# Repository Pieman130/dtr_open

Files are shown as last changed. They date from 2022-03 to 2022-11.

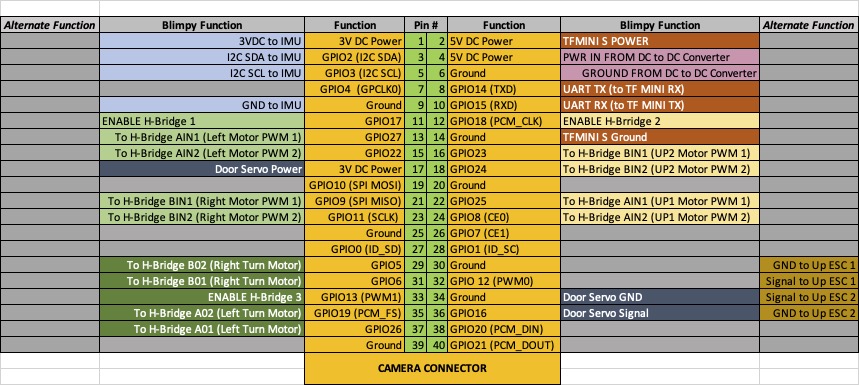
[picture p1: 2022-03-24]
images/Rpi2_pinout.jpg

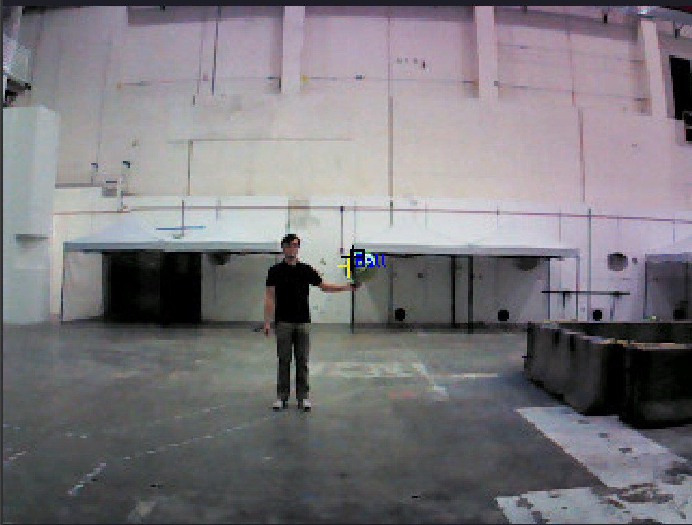
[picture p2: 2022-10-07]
images/Color Detection Metrics Videos/Test Example Photo.png

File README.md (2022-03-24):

More info in wiki: [DTR Wiki](https://github.iu.edu/DTR/dtr/wiki)

`blimpy.py` is the main Blimp script

`IMU_test.py` to run simple tests to ensure BNO055 IMU is functioning

`LIDAR_test.py` tests for TFMini lidar using UART connection

`manual_control.py` to operate blimp with only PS3 controller (no autonomy)  Note: deadman switch is disabled 

**NOTE: the BNO055 library requires two updates:**
1) Ensure software I2C is enabled and HW I2C is disabled on the raspberry pi
	1) modify `/boot/config.txt` to include this line:
	
	`dtoverlay=i2c-gpio,bus=3,i2c_gpio_sda=23,i2c_gpio_scl=24`
	
	2) comment this line out if not already done:

	`dtparam=i2c_arm=on`

2) You may need to modify `bno055.py` to add support for software i2c bus.  On line 196 `self._bus = smbus.SMBus(1)` change the 1 to a 3

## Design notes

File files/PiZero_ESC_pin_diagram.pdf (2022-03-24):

Alternate Function | Blimpy Function | Function | Pin # | Function | Blimpy Function | Alternate Function
| 3VDC to IMU | 3V DC Power | 1 | 2 | 5V DC Power | TFMINI S POWER | Additional wire to Vin Ultrasonic Sensor
| I2C SDA to IMU | GPIO2 (I2C SDA) | 3 | 4 | 5V DC Power | PWR IN FROM DC to DC Converter
| I2C SCL to IMU | GPIO3 (I2C SCL) | 5 | 6 | Ground | GROUND FROM DC to DC Converter
| | GPIO4 (GPCLK0) | 7 | 8 | GPIO14 (TXD) | UART TX (to TF MINI RX)
| GND to IMU | Ground | 9 | 10 | GPIO15 (RXD) | UART RX (to TF MINI TX)
| | GPIO17 | 11 | 12 | GPIO18 (PCM_CLK)
| | GPIO27 | 13 | 14 | Ground | TFMINI S Ground
| Door Servo Signal | GPIO22 | 15 | 16 | GPIO23 | Ultrasonic TRIG
| Door Servo Power | 3V DC Power | 17 | 18 | GPIO24 | Ultrasonic ECHO
| | GPIO10 (SPI MOSI) | 19 | 20 | Ground
| | GPIO9 (SPI MISO) | 21 | 22 | GPIO25
| | GPIO11 (SCLK) | 23 | 24 | GPIO8 (CE0)
| Door Servo GND | Ground | 25 | 26 | GPIO7 (CE1) | Thrust Motor
| | GPIO0 (ID_SD) | 27 | 28 | GPIO1 (ID_SC)
| | GPIO5 | 29 | 30 | Ground
| | GPIO6 | 31 | 32 | GPIO 12 (PWM0) | Altitude Front Motor
| | GPIO13 (PWM1) | 33 | 34 | Ground
| | GPIO19 (PCM_FS) | 35 | 36 | GPIO16 | Altitude Rear Motor
| | GPIO26 | 37 | 38 | GPIO20 (PCM_DIN) | Steer Motor
| | Ground | 39 | 40 | GPIO21 (PCM_DOUT) | Steer Servo
CAMERA CONNECTOR

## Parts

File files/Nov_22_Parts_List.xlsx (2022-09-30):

Need | Item | Quantity Rqd* | Quantity OH | Source | Note
 | Store Purchased
X | Small Carbon Fiber Rods | 13 | 8 | https://www.amazon.com/gp/product/B07P81VC34/ref=sw_img_1?smid=A1THAZDOWP300U&th=1 | Come in packes of 10
 | Large Carbon Fiber Rods | 7 | 11 | https://www.amazon.com/gp/product/B07V2J6YSR/ref=ppx_yo_dt_b_asin_title_o07_s00?ie=UTF8&th=1 | Come in packs of 4
X | 1200mAh Battery | 1 | 1 | https://www.amazon.com/dp/B09K7VLDN5?psc=1&ref=ppx_yo2ov_dt_b_product_details | Come in packs of 2
 | Servo | 1 | 2 | https://www.amazon.com/FLASH-HOBBY-Steering-Interface-Aircraft/dp/B08NPHG99D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 | We actually have a lot more in the drawer
 | RC Receiver | 1 | 1 | https://www.amazon.com/gp/product/B01N5INCBH/ref=ppx_yo_dt_b_asin_title_o07_s01?ie=UTF8&psc=1 | 1 Rcvr shared between craft
 | OpenMV Carmera | 1 | 1 | https://www.sparkfun.com/products/18982 | vers H7 (out of stock most places)
 | ESC | 3 | 5 | https://www.amazon.com/gp/product/B09F3G4KNB/ref=ppx_yo_dt_b_asin_title_o01_s00?ie=UTF8&psc=1 | Come in packs of 4
 | Motors | 3 | 4 | https://www.amazon.com/gp/product/B07XR8GYT5/ref=ppx_yo_dt_b_asin_title_o01_s02?ie=UTF8&psc=1 | Come in packs of 4
 | Props | 3 | 10+ | https://www.amazon.com/gp/product/B087CX2JYG/ref=ppx_yo_dt_b_asin_title_o01_s02?ie=UTF8&psc=1 | Come in packs of 16
 | Lidar | 1 | 2 | https://www.amazon.com/dp/B08D1XVRV5?aaxitk=5ca1cb0fbe332688bafaf63f109873fa&hsa_cr_id=7103712130501
 | JST-PH 2,0 Connectors | 4 | 5+ | https://www.amazon.com/Upgraded-Connector-Battery-Inductrix-Eachine/dp/B07NWD5NTN?s=electronics | Come in packs of 5
 | PixRacer | 1 | 1 | https://store.mrobotics.io/mRo-PixRacer-R14-Official-p/auav-pxrcr-r14-mr.htm | Out of stock everywhere
 | Wire (various colors) | As Needed | Probably Enough | https://www.amazon.com/Fermerry-Stranded-Silicone-Cables-Electrical/dp/B089CP9N98 | Should have enough of each color on hand
 | GH 1.25 Connectors | 1 | 1 | https://www.amazon.com/gp/product/B07PBHN7TM/ref=ppx_yo_dt_b_asin_title_o05_s06?ie=UTF8&psc=1 | Still have half the box on hand
 | DC to DC Converter | 1 | 1 | https://www.amazon.com/Converter-DROK-Adjustable-Transformer-Stabilizer/dp/B08Q3PMJTT | Original purchased model no longer available
X | Blue Balloons | 4 | 0 | https://balloonsfast.com/big-round-balloons-mylar-36-inch-blue-foil-circle-balloon-12679.html
 | Red Balloons | 0 | 4 | https://www.balloons123.com/products/36-round-ruby-red-foil-foil-balloon?variant=422858981403&currency=USD
 | 3D printed parts
 | Catcher - "Y" corners | 5 | 5 | collin_corner_connector1 v2.stl
 | Catcher - "T" connector | 4 | 6 | Collin_Support Connector v1 v2.stl
 | Catcher - Straight Connector | 5 | 10 | Collin_Straight Connector v1 v3.stl
 | Large Ballon Coupler | 4 | 4 | ??
 | Small Balloon Coupler | 2 | 4 | balloon coupler v4.stl
X | Basket to Balloon mount | 4 | 0 | Catcher Mount v1.stl
X | Wire Clips | 8 | 1 | wire clips v2.stl
 | Thrust/Yaw Mount | 1 | 1 | Thrust_Yaw Mount v5.stl
X | Lidar Mount | 1 | 0 | TFMini mount v2.stl
X | Battery Mount | 1 | 0 | Collin_Battery_Holder_Square v2 v2.stl
 | Pixracer Mount | 1 | 1 | PixRacer Mount v2.stl
 | Up Motor Mount | 1 | 4 | flat_mount.stl
X | OpenMV Mount | 1 | 0 | openMV Mount v2.stl
X | ESC Mount | 3 | 2 | esc clip v2.stl
 | Large Tube Coupler | 2 | 6 | ??
 | Large "X" Coupler | 2 | 5 | ??
 | Custom PCB Parts
 | OpenMV Shield | 1 | 1 | Custom made - TODO - breakout individual parts
 | IR Detector | 1 | 1 | Custom made - TODO breakout individual parts
 | *Quantity Rqd is per craft

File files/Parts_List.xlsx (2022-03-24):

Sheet: Basic_Kit
Component | Qty | Cost | Subotal | Link | Min Qty
Camera | 1 | 69.95 | 69.95 | https://www.robotshop.com/en/openmv-cam-h7-r2-image-sensor.html | 1
Camera | 1 | 0 | 0 | Alternate Cameras?
Servos | 1 | 12.65 | 12.65 | https://www.amazon.com/FLASH-HOBBY-Steering-Interface-Aircraft/dp/B08NPHG99D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 | 1
Motors | 1 | 9.95 | 9.95 | https://www.amazon.com/4pcs-Coreless-Brushed-Motor-7x16mm/dp/B08LV5HK8D | 1
Props | 1 | 11.99 | 11.99 | https://www.amazon.com/Propellers-Replacement-Eachine-Inductrix-Quadcopter/dp/B079DP3V42 | 1
Remote | 1 | 12.99 | 12.99 | https://www.amazon.com/VOYEE-PS3-Controller-Wireless-Rechargable/dp/B07TYR1MDV | 1
Tape | 1 | 10.99 | 10.99 | https://www.amazon.com/Double-Double-Sided-Adhesive-Scrapbook-Display/dp/B087QYVCPW | 1
Driver | 1 | 7.49 | 7.49 | https://www.pololu.com/product/2135 | 1
Connectors | 1 | 21.99 | 21.99 | https://www.amazon.com/Pre-Crimped-Connectors-SPRacingF3-Omnibus-Silicone/dp/B07PDQKHJ2 | 1
Connectors | 1 | 6.99 | 6.99 | https://www.amazon.com/gp/product/B013JRWCBU | 1
Connectors | 1 | 7.59 | 7.59 | https://www.amazon.com/Micro-2-Pin-Connector-100Mm-Female/dp/B01DUC1I7S?s=electronics | 1
Connectors | 1 | 20.99 | 20.99 | https://www.amazon.com/Pre-Crimped-Connectors-Pixhawk2-Pixracer-Silicone/dp/B07PBHN7TM | 1
Conenctors | 1 | 12.19 | 12.19 | https://www.amazon.com/Connectors-1-25MM-Female-Connector-Cables/dp/B073WPQLVX?s=electronics | 1
Controller | 1 | 10 | 10 | https://www.mouser.com/ProductDetail/Espressif-Systems/ESP32-DevKitC-32D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 | 1
Controller | 1 | 9.59 | 9.59 | https://www.amazon.com/Raspberry-Microcontroller-Development-Dual-Core-Processor/dp/B08TN4VLN7
Controller | 1 |  | 0 | Alternate Microcontrollers?
Battery | 6 | 7.95 | 47.7 | https://www.adafruit.com/product/1578 | 4
Charger | 2 | 6.95 | 13.9 | https://www.adafruit.com/product/1905 | 2
Air Swimmer | 4 | 39.99 | 159.96 | https://www.amazon.com/Air-Swimmer-Inflatable-Flying-Shark/dp/B00658LN3E | 2
PI Camera | 1 | 13.99 | 13.99 | https://www.amazon.com/Camera-Arducam-Raspberry-Raspbian-MotionEye/dp/B01LY05LOE
PI Zero W | 1 | 33.99 | 33.99 | https://www.amazon.com/Vilros-Raspberry-Starter-Official-Case-Power/dp/B0787BXR3P
Total |  |  | 494.89
Number of total kits |  | 5 | 2474.45

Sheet: Sheet2
halow hat for ferry/mesh |  | https://store.rokland.com/collections/802-11ah-wi-fi-halow/products/alfa-network-ahpi7292s-ieee-802-11ah-sub-1-ghz-module-in-raspberry-pi-hat-form-factor
5VDC Boost Module |  | https://www.adafruit.com/product/4654
JST PH Cable |  | https://www.adafruit.com/product/3814
mylar |  | http://film.fluffyscarsdale.com/
Distance Sensor |  | https://www.sparkfun.com/products/14722
IMU |  | https://www.sparkfun.com/products/15335
QWiic Cable |  | https://www.sparkfun.com/products/17258
meshable wifi dongle | 5.99 | https://www.amazon.com/gp/product/B00ZQ0C4KI
 |  | https://store.mrobotics.io/mRo-PixRacer-R15-Official-p/m10023a.htm
 |  | https://www.amazon.com/Fermerry-Stranded-Silicone-Cables-Electrical/dp/B089CP9N98
 |  | https://www.amazon.com/StrivedayTM-Flexible-Silicone-electronic-electrics/dp/B01KQ2JNLI
 |  | https://www.amazon.com/Electronix-Express-Assorted-Gauges-Magnet/dp/B01D4ZHXPC
 |  | https://www.amazon.com/Oralite-Microprismatic-Retroreflective-Conspicuity-Tape/dp/B0041PCG2A?th=1
 |  | https://www.walmart.com/ip/Oralite-Reflexite-V98-Microprismatic-Conspicuity-Tape-2-in-x-15-ft-Fluorescent-Orange/101885580
 |  | https://www.amazon.com/Aluminum-Balloons-Self-Sealing-Metallic-Hangable/dp/B07YD7PLC7?s=toys-and-games
 |  | https://www.amazon.com/RIKIMARU-Abrasion-Resistant-Superline-Diameter/dp/B07Q7Y6TD4

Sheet: 2nd order
Qty | Cost | Subtotal | Link
2 | $149.90 | $299.80 | https://store.mrobotics.io/mRo-PixRacer-R15-Official-p/m10023a.htm
2 | $69.97 | $139.94 | https://store.rokland.com/collections/802-11ah-wi-fi-halow/products/alfa-network-ahpi7292s-ieee-802-11ah-sub-1-ghz-module-in-raspberry-pi-hat-form-factor
12 | $7.95 | $95.40 | https://www.adafruit.com/product/1578
4 | $6.95 | $27.80 | https://www.adafruit.com/product/1905
10 | $0.75 | $7.50 | https://www.adafruit.com/product/3814
4 | $3.56 | $14.24 | https://www.adafruit.com/product/4654
3 | $9.95 | $29.85 | https://www.amazon.com/4pcs-Coreless-Brushed-Motor-7x16mm/dp/B08LV5HK8D
12 | $39.99 | $479.88 | https://www.amazon.com/Air-Swimmer-Inflatable-Flying-Shark/dp/B00658LN3E
2 | $8.99 | $17.98 | https://www.amazon.com/Aluminum-Balloons-Self-Sealing-Metallic-Hangable/dp/B07YD7PLC7?s=toys-and-games
3 | $13.99 | $41.97 | https://www.amazon.com/Camera-Arducam-Raspberry-Raspbian-MotionEye/dp/B01LY05LOE
1 | $39.99 | $39.99 | https://www.amazon.com/Electronix-Express-Assorted-Gauges-Magnet/dp/B01D4ZHXPC
1 | $16.99 | $16.99 | https://www.amazon.com/Fermerry-Stranded-Silicone-Cables-Electrical/dp/B089CP9N98
5 | $12.65 | $63.25 | https://www.amazon.com/FLASH-HOBBY-Steering-Interface-Aircraft/dp/B08NPHG99D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
6 | $5.99 | $35.94 | https://www.amazon.com/gp/product/B00ZQ0C4KI
1 | $33.26 | $33.26 | https://www.amazon.com/Oralite-Microprismatic-Retroreflective-Conspicuity-Tape/dp/B0041PCG2A?th=1
1 | $37.68 | $37.68 | https://www.amazon.com/Oralite-Reflexite-Microprismatic-Retroreflective-Conspicuity/dp/B0041PI10G
2 | $11.99 | $23.98 | https://www.amazon.com/Propellers-Replacement-Eachine-Inductrix-Quadcopter/dp/B079DP3V42
3 | $9.59 | $28.77 | https://www.amazon.com/Raspberry-Microcontroller-Development-Dual-Core-Processor/dp/B08TN4VLN7
1 | $14.98 | $14.98 | https://www.amazon.com/RIKIMARU-Abrasion-Resistant-Superline-Diameter/dp/B07Q7Y6TD4
1 | $12.99 | $12.99 | https://www.amazon.com/StrivedayTM-Flexible-Silicone-electronic-electrics/dp/B01KQ2JNLI
4 | $33.99 | $135.96 | https://www.amazon.com/Vilros-Raspberry-Starter-Official-Case-Power/dp/B0787BXR3P
4 | $10.00 | $40.00 | https://www.mouser.com/ProductDetail/Espressif-Systems/ESP32-DevKitC-32D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
4 | $7.49 | $29.96 | https://www.pololu.com/product/2135
2 | $69.95 | $139.90 | https://www.robotshop.com/en/openmv-cam-h7-r2-image-sensor.html
4 | $21.95 | $87.80 | https://www.sparkfun.com/products/14722
4 | $16.95 | $67.80 | https://www.sparkfun.com/products/15335
20 | $1.50 | $30.00 | https://www.sparkfun.com/products/17258
3 | $34.14 | $102.42 | https://www.walmart.com/ip/Sony-PlayStation-3-Dualshock-3-Wireless-Controller-with-Battery-Black-Refurbished/385280998
Subtotal |  | $2096.03
Mylar Order
http://film.fluffyscarsdale.com/home.html
Email: FluffyScarsdale@gmail.com
Procedure for ordering is email Fluffy with order, shipping address, and payment information
Qty | Cost | Subtotal | Item
20-yd | 3.50/yd | $70.00 | 44" Red Mylar Film
20-yd | 3.50/yd | $70.00 | 44" Blue Mylar Film
Subtotal |  | $140.00
 |  | RPi Replacement | https://www.amazon.com/CanaKit-Raspberry-Wireless-Complete-Starter/dp/B072N3X39J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
 |  | Dongle | https://smile.amazon.com/gp/product/B00BWT1IFE

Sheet: 3rd Order
Qty | Cost | Subtotal | Link
6 | $65.99 | $395.94 | https://www.amazon.com/gp/product/B07XR8GYT5/ref=ppx_yo_dt_b_asin_title_o01_s00?ie=UTF8&psc=1
3 | $12.99 | $38.97 | https://www.amazon.com/gp/product/B087CX2JYG/ref=ppx_yo_dt_b_asin_title_o01_s00?ie=UTF8&psc=1
6 | $27.99 | $167.94 | https://www.amazon.com/gp/product/B09Q2TPDL7/ref=ppx_yo_dt_b_asin_title_o01_s01?ie=UTF8&psc=1
2 | $12.99 | $25.98 | https://www.amazon.com/gp/product/B0823QLMWC/ref=ppx_yo_dt_b_asin_title_o01_s01?ie=UTF8&psc=1
1 | $14.99 | $14.99 | https://www.amazon.com/WMYCONGCONG-HC-SR04-Ultrasonic-Distance-Measuring/dp/B07JJHCVRG?s=electronics
6 | $40.86 | $245.16 | https://www.amazon.com/gp/product/B09F3G4KNB/ref=ppx_yo_dt_b_asin_title_o01_s02?ie=UTF8&psc=1
4 | $19.90 | $79.60 | https://www.amazon.com/Espressif-ESP-Eye-Development-Board/dp/B087T5GYHJ
Subtotal |  | $968.58

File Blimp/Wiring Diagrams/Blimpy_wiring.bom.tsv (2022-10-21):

Id | Description | Qty | Unit | Designators
1 | Cable, 1 x 28 AWG | 49.0 | in | Lift ESC Signal Cable, Thrust ESC Signal Cable, Yaw ESC Signal Cable
2 | Cable, 2 x 22 AWG | 45.0 | in | Battery Distribution Cable 1, Battery Distribution Cable 2, Mid ESC Power Cable, Rear ESC Power Cable, Regulator 5V to Pixracer Cable, Regulator to Battery Cable
3 | Cable, 3 x 28 AWG | 66.0 | in | CatchServoCable, DetectorCable, RCCable
4 | Cable, 4 x 22/28 AWG | 28.0 | in | PixOpenMVCable
5 | Cable, 4 x 28 AWG | 6.0 | in | LIDARCable
6 | Connector, 0.1" header, female, 3 pins | 8 |  | IR-Detector, Lift ESC Signal, OpenMV_Hat-Detector, OpenMV_Hat-Servo1 - Top, OpenMV_Hat-Servo3 - Bottom, RC_Receiver, Thrust ESC Signal, Yaw ESC Signal
7 | Connector, 0.1" header, female, 4 pins | 1 |  | OpenMV_Hat-Serial
8 | Connector, 0.1" header, female, 6 pins | 1 |  | Pixracer-Servos
9 | Connector, JST 1.25, male, 3 pins | 1 |  | Catch Servo
10 | Connector, JST-GH_1.25, female, 4 pins | 1 |  | LIDAR-Serial
11 | Connector, JST-GH_1.25, female, 5 pins | 1 |  | Pixracer-RC
12 | Connector, JST-GH_1.25, female, 6 pins | 3 |  | Pixracer-PWR, Pixracer-Telem1, Pixracer-Telem2
13 | Connector, JST-PH 2.0, female, 2 pins | 3 |  | Battery-Reg, Lift ESC Power, Yaw and Thrust ESC Power
14 | Connector, JST-PH 2.0, male, 2 pins | 4 |  | Battery, Mid ESC Power, Rear ESC Power, Reg-Power
15 | Connector, solder lead | 6
16 | Connector, solder pad, 3 pins | 1 |  | 5VRegulator

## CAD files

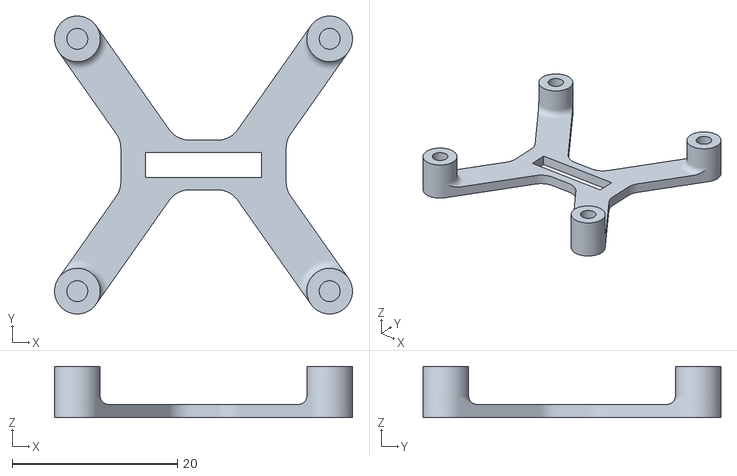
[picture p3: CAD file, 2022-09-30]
Blimp/3D Print Models/PixRacer Mount v3_PixRacer Mount v3_Body1.stl
36.0 x 36.0 x 6.20

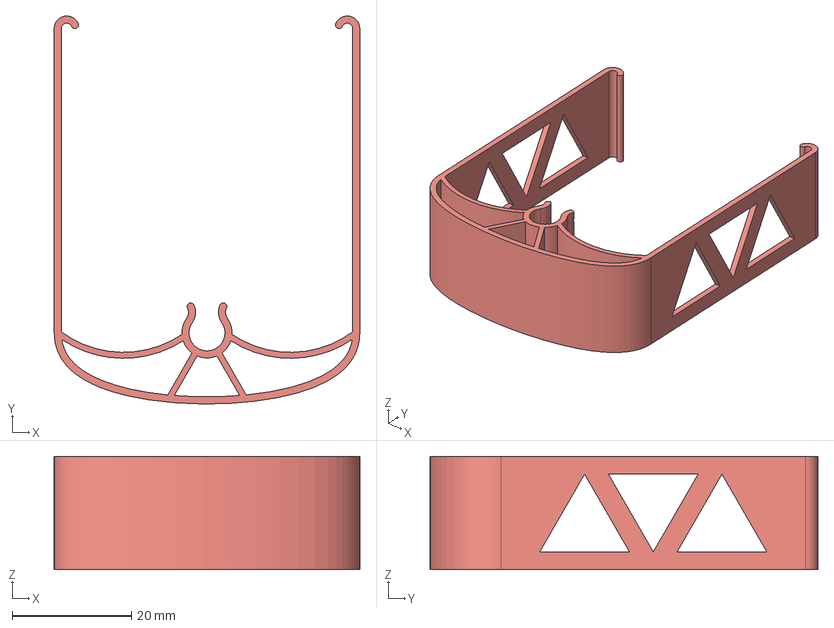
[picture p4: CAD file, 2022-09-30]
Blimp/3D Print Models/balloon coupler v6.step
51.2 x 65.0 x 19.0 mm

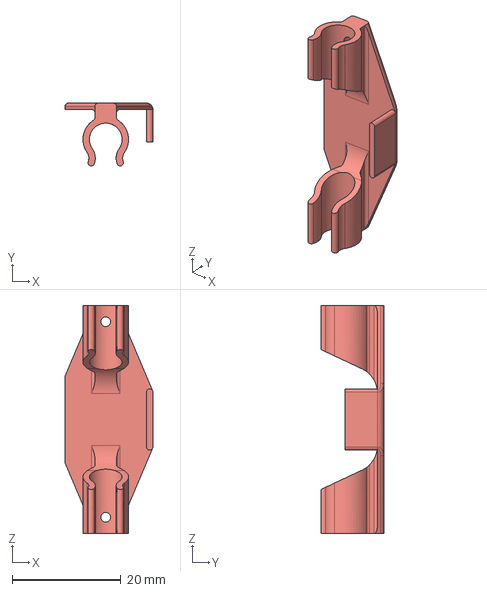
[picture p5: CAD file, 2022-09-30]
Blimp/3D Print Models/TFMini mount v3.step
16.2 x 11.6 x 42.0 mm

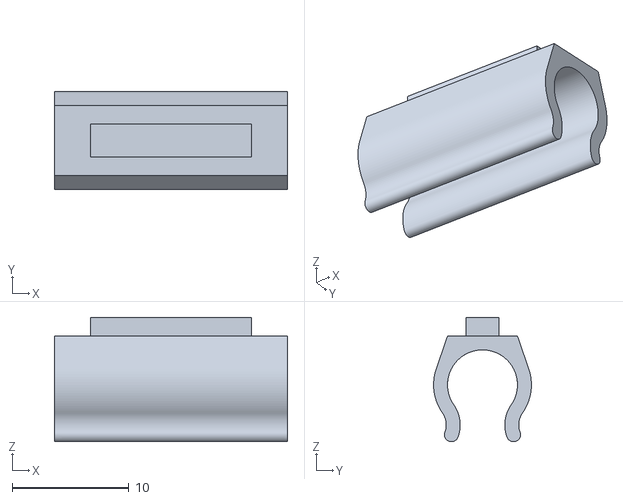
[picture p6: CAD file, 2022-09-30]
Blimp/3D Print Models/PixRacer Mount v3_PixRacer Mount v3_Component1_1_Body1.stl
20.0 x 8.40 x 10.7

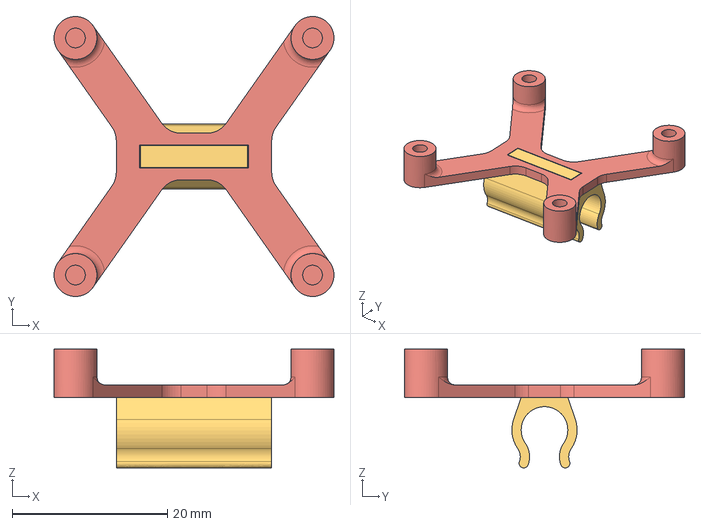
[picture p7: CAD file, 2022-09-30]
Blimp/3D Print Models/PixRacer Mount v3.step
36.0 x 36.0 x 15.3 mm

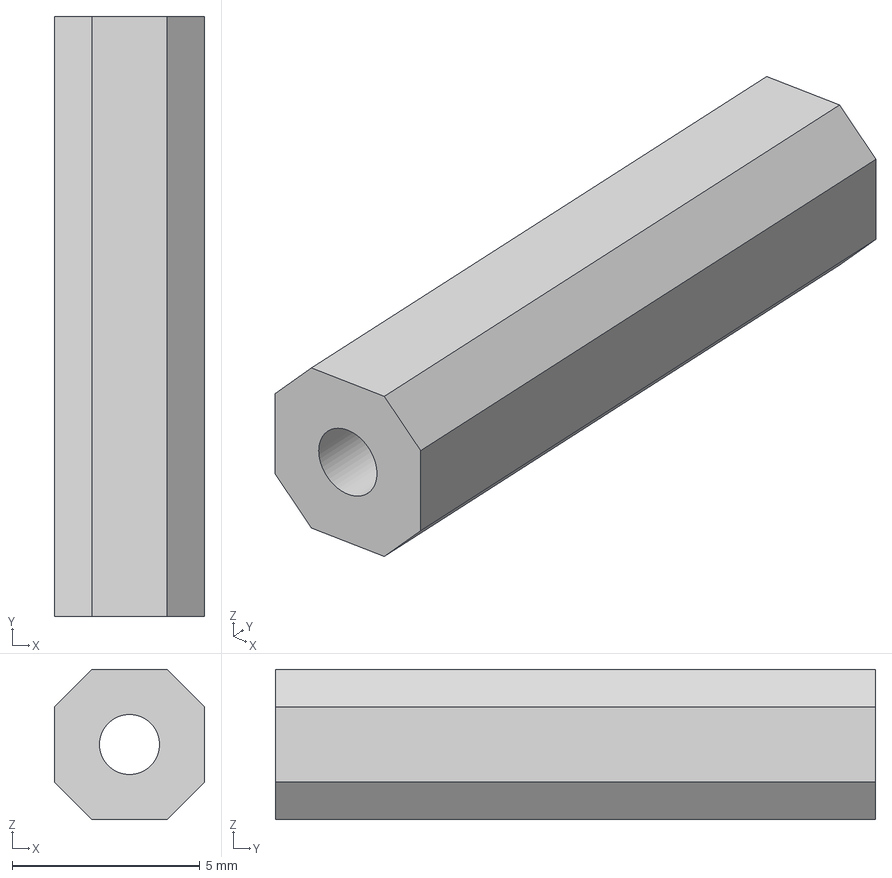
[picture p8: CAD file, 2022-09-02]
Blimp/3D Print Models/Collin_Straight Connector v1 v3.step
4.00 x 16.0 x 4.00 mm

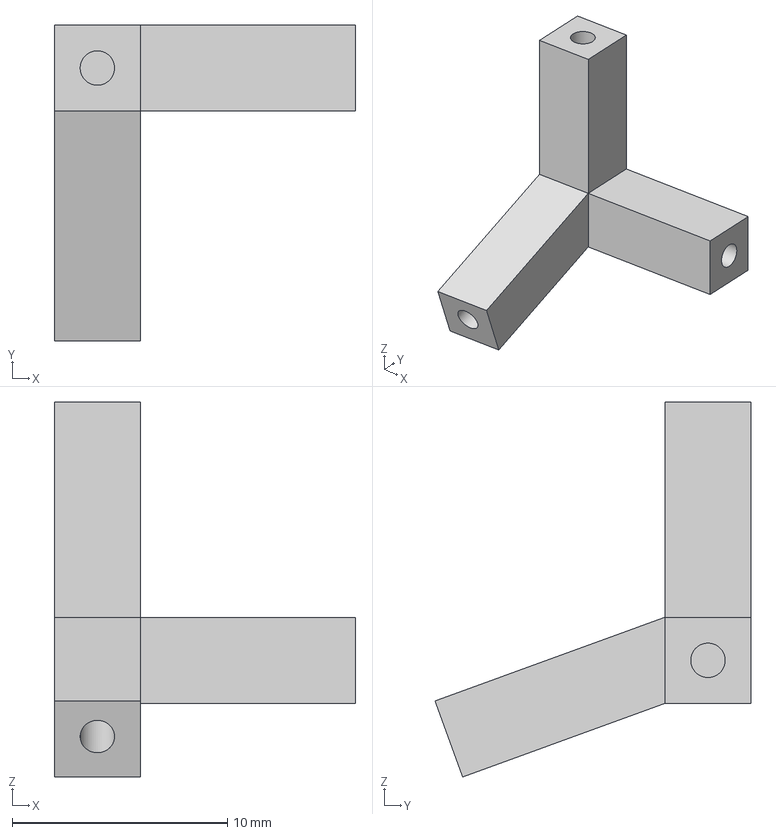
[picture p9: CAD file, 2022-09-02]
Blimp/3D Print Models/Collin_Corner Connector 1 v2 v1.step
14.0 x 14.7 x 17.4 mm

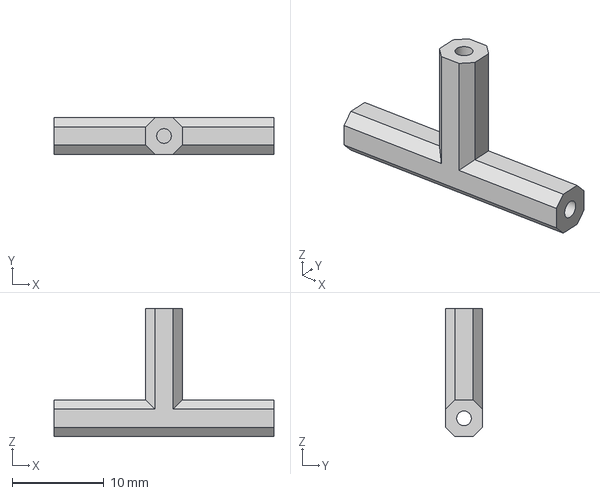
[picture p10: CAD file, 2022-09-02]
Blimp/3D Print Models/Collin_Support Connector v1 v2.step
24.0 x 4.00 x 14.0 mm

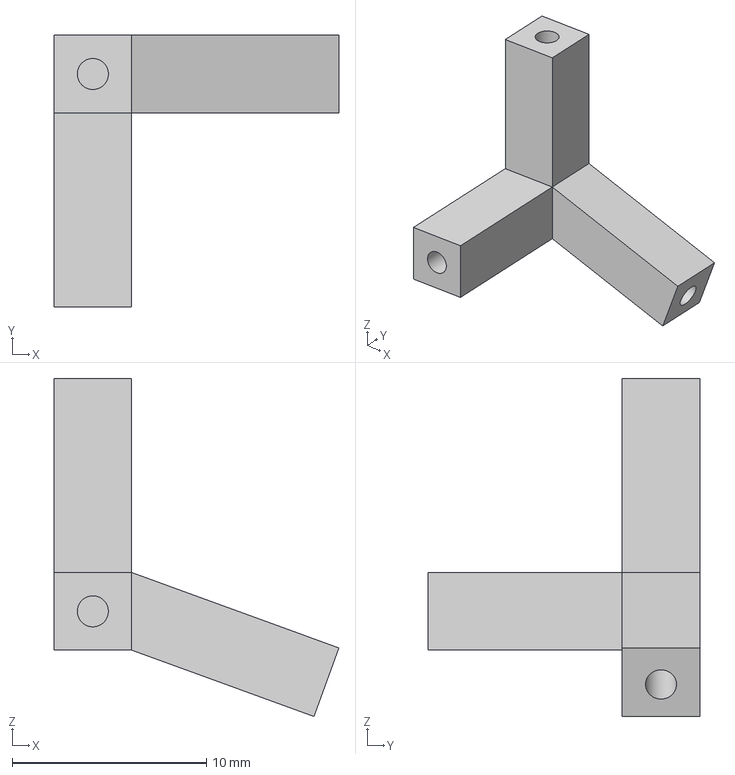
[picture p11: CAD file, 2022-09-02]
Blimp/3D Print Models/Collin_Corner Connector 2 v1 v1.step
14.7 x 14.0 x 17.4 mm

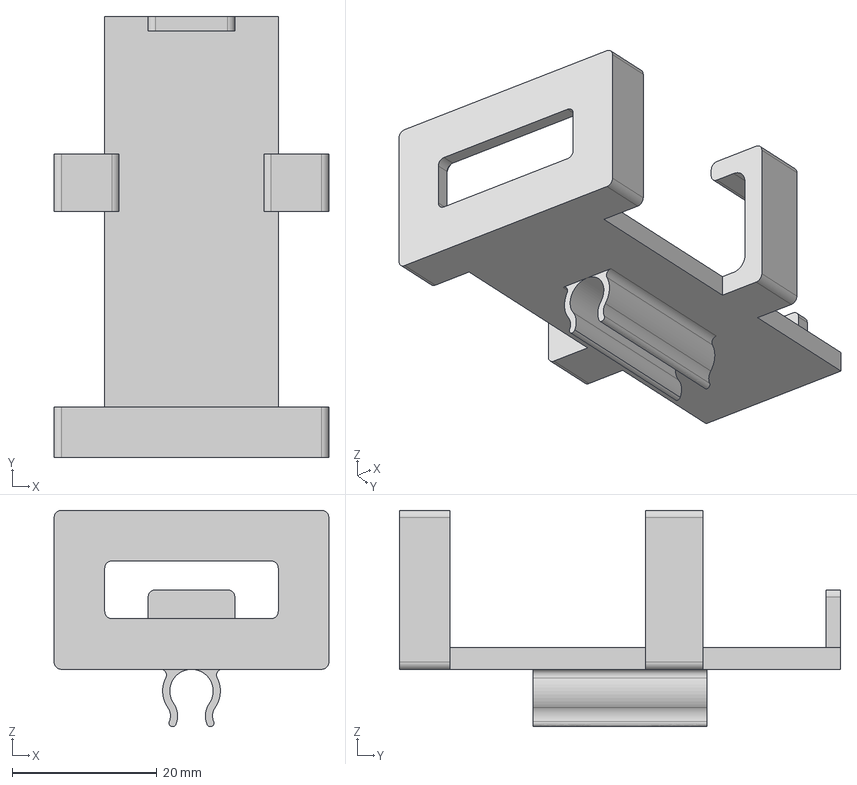
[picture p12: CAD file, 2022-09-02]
Blimp/3D Print Models/Collin_Battery_Holder_Square v2 v2.step
38.0 x 61.0 x 29.9 mm

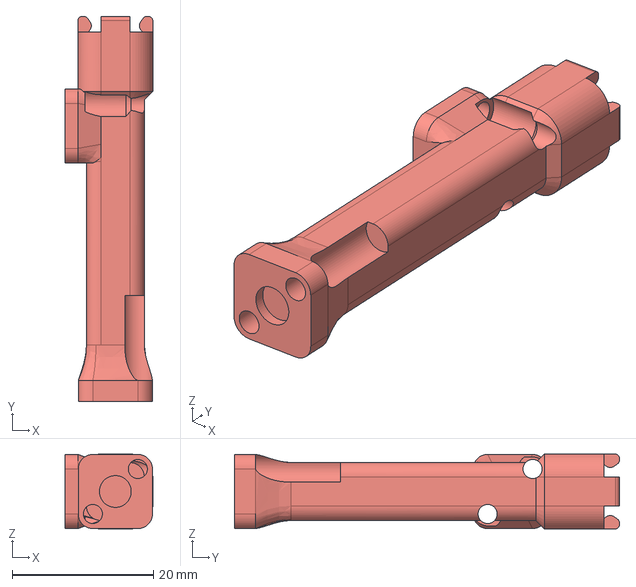
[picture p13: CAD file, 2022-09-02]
Blimp/3D Print Models/Thrust_Yaw Mount v5.step
12.4 x 54.5 x 10.6 mm
Tube Stop
Motor Mount

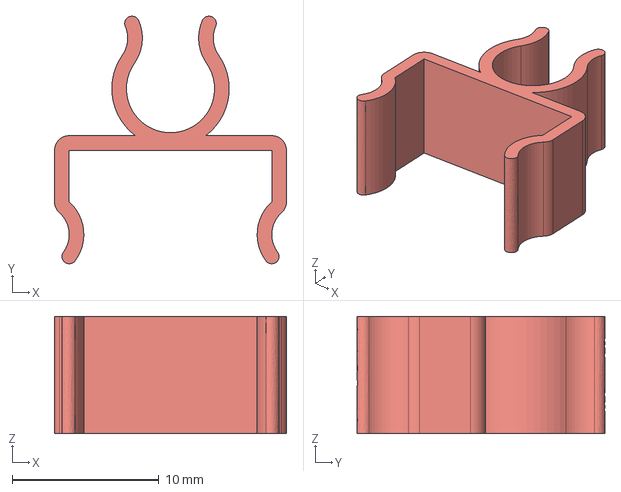
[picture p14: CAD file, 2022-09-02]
Blimp/3D Print Models/esc clip v2.step
15.8 x 16.9 x 8.00 mm

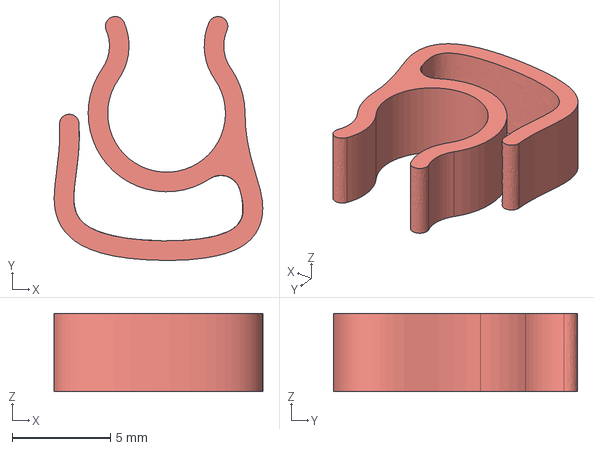
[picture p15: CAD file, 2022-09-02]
Blimp/3D Print Models/wire clips v2.step
10.6 x 12.4 x 4.00 mm

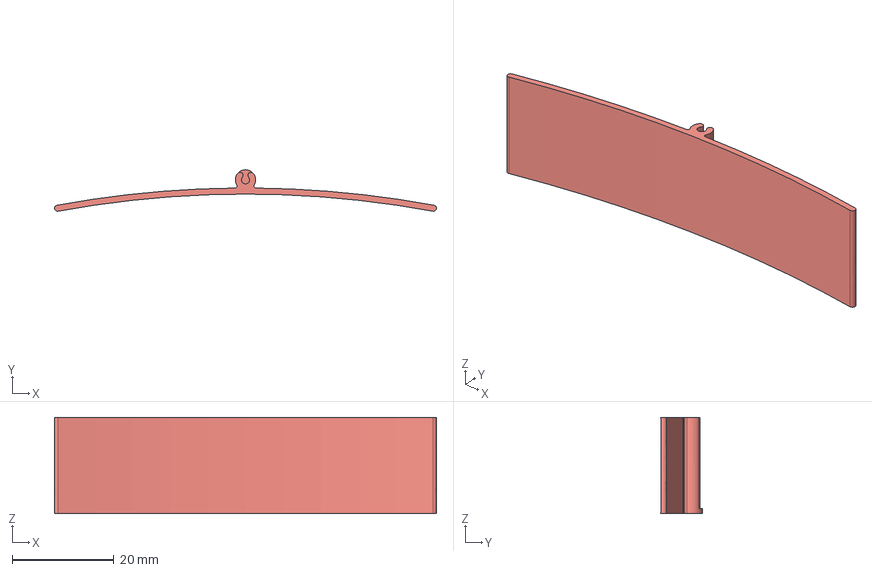
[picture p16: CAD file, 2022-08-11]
Blimp/3D Print Models/Catcher Mount v1.step
75.2 x 8.19 x 19.0 mm

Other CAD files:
Blimp/3D Print Models/openMV Mount v2.step
Blimp/3D Print Models/flat_mount.stl
Blimp/3D Print Models/right_angle_mount.stl
Blimp/3D Print Models/servo_mount.stl
Blimp/3D Print Models/Catcher Mount v1.f3d
Blimp/3D Print Models/Catcher Mount v1.stl
Blimp/3D Print Models/Collin_Battery_Holder_Square v2 v2.f3d
Blimp/3D Print Models/Collin_Battery_Holder_Square v2 v2.stl
Blimp/3D Print Models/Collin_Corner Connector 1 v2 v1.f3d
Blimp/3D Print Models/Collin_Corner Connector 1 v2 v1.stl
Blimp/3D Print Models/Collin_Corner Connector 2 v1 v1.f3d
Blimp/3D Print Models/Collin_Corner Connector 2 v1 v1.stl
Blimp/3D Print Models/Collin_Straight Connector v1 v3.f3d
Blimp/3D Print Models/Collin_Straight Connector v1 v3.stl
Blimp/3D Print Models/Collin_Support Connector v1 v2.f3d
Blimp/3D Print Models/Collin_Support Connector v1 v2.stl
Blimp/3D Print Models/PixRacer Mount v3.f3d
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

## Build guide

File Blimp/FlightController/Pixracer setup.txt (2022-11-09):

Pixracer FC Setup
Install Mission planner
Connect pixracer to computer over USB
In MissionPlanner, to Setup, Install Firmware
Load Arduplane V4.2.3 OFFICIAL, select platform Pixracer-bdshot

Click connect (may have to change COM Ports)
Go to Config, Full Param Tree.
Load from File (on right) and select ArudPlaneConfiguredParams.param file

ESC Flashing
Use the standard arduplane configured parameters
Disconnect mission planner, safety button should be disarmed (blinking rapidly)
Ensure ESCs have power
go to https://esc-configurator.com/ and connect to com port
If connection successful, there should be 4 motors listed under Motor Control (regardless of how many actually connected.)
Click Read Settings

Configure ESCs as:
Motor Direction: Bidirectional
PPM Min Throttle: 1100us
PPM Max Throttle: 1900us
escPPMCenterThrottle: 1500us

Click Write Settings
Click Read Settings and ensure that settings stuck for all ESCs

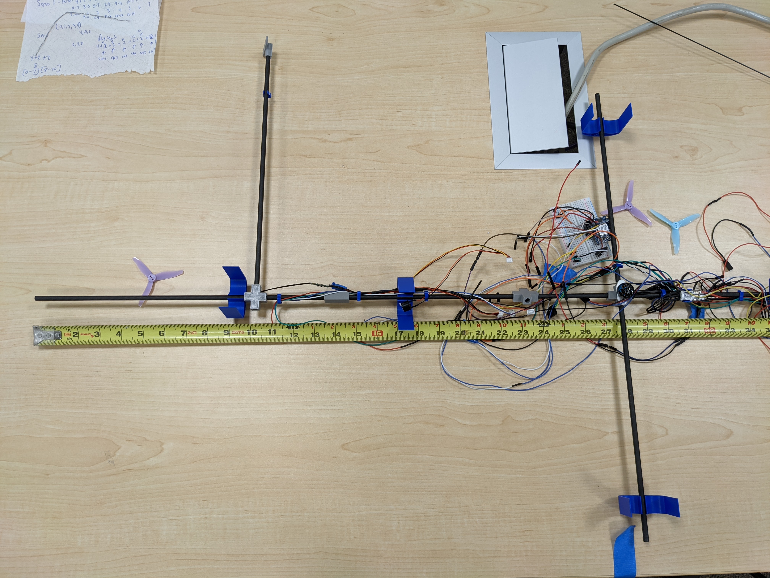
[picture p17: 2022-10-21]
Blimp/Assembly Photos/PXL_20220826_192233887.jpg

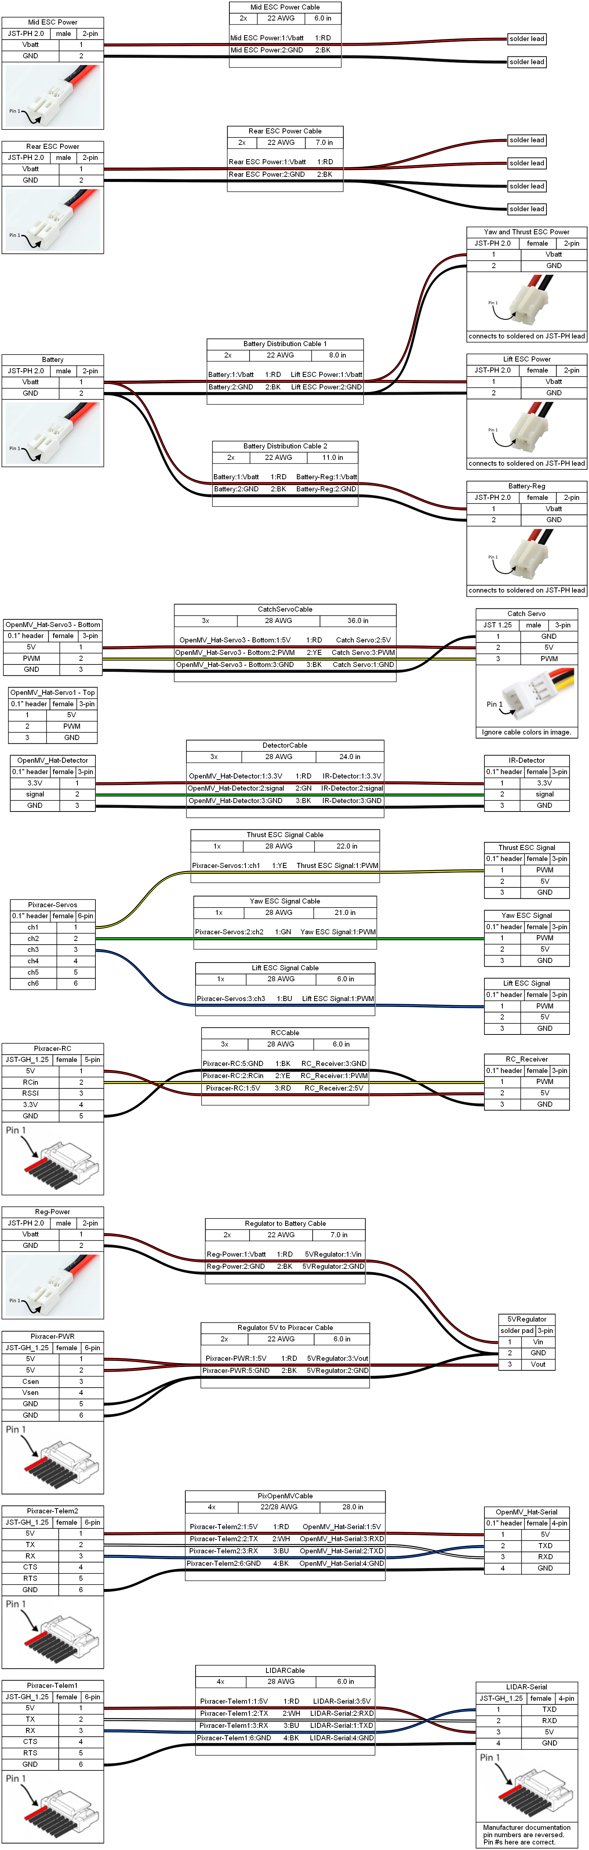
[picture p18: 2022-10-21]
Blimp/Wiring Diagrams/Blimpy_wiring.png

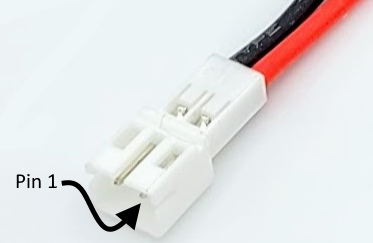
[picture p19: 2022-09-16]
Blimp/Wiring Diagrams/JST-PH 2.0 Pin ID.png

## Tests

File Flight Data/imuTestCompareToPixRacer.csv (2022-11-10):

logTime | yawMotor | p_yaw | i_yaw | d_yaw | scalar_yaw | loopTime | controlAuthority | currentManeuver | state_description | state_target | state_action | imu_yaw | imu_yaw_rate | imu_yaw_limited | imu_yaw_rate_limited | loopTime
2022-11-09 13:43:35.030 | 0 | 0.5 | 0 | 0 | 1 | 0.199219 | None | Do nothing. | rcRemote | none | none | -1.58723 | 0.000208111 | -1.58723 | 0.000208111 | 0.199219
2022-11-09 13:43:34.823 | 0 | 0.5 | 0 | 0 | 1 | 0.210937 | None | Do nothing. | rcRemote | none | none | -1.58723 | 0.000208111 | -1.58723 | 0.000208111 | 0.210937
2022-11-09 13:43:34.617 | 0 | 0.5 | 0 | 0 | 1 | 0.199219 | None | Do nothing. | rcRemote | none | none | -1.58723 | 0.000208111 | -1.58723 | 0.000208111 | 0.199219
2022-11-09 13:43:34.407 | 0 | 0.5 | 0 | 0 | 1 | 0.203125 | None | Do nothing. | rcRemote | none | none | -1.58723 | 0.000208111 | -1.58723 | 0.000208111 | 0.203125
2022-11-09 13:43:34.200 | 0 | 0.5 | 0 | 0 | 1 | 0.222656 | None | Do nothing. | rcRemote | none | none | -1.5875 | 0.00174988 | -1.5875 | 0.00174988 | 0.222656
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

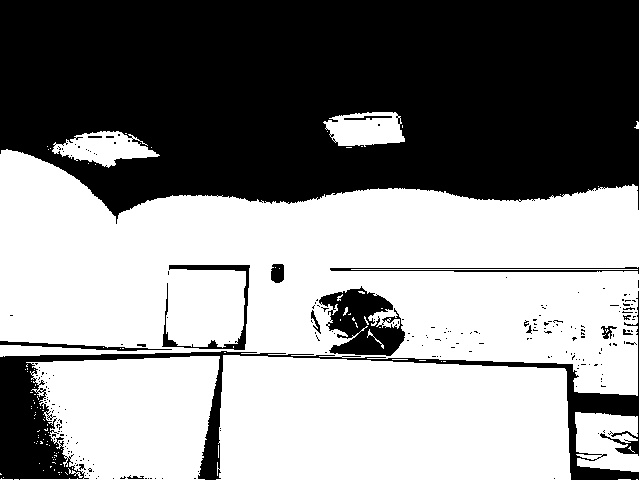
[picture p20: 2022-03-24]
Blimp/object_detection_openCV/test_images/HUE_10_90.jpg

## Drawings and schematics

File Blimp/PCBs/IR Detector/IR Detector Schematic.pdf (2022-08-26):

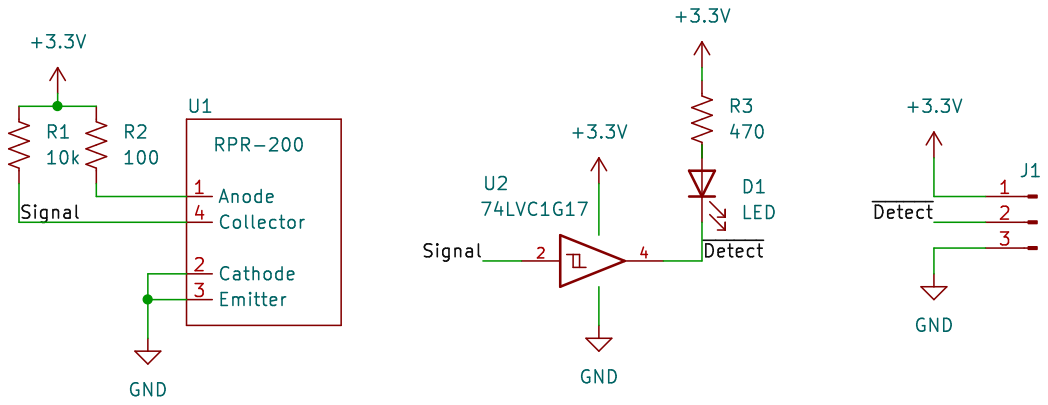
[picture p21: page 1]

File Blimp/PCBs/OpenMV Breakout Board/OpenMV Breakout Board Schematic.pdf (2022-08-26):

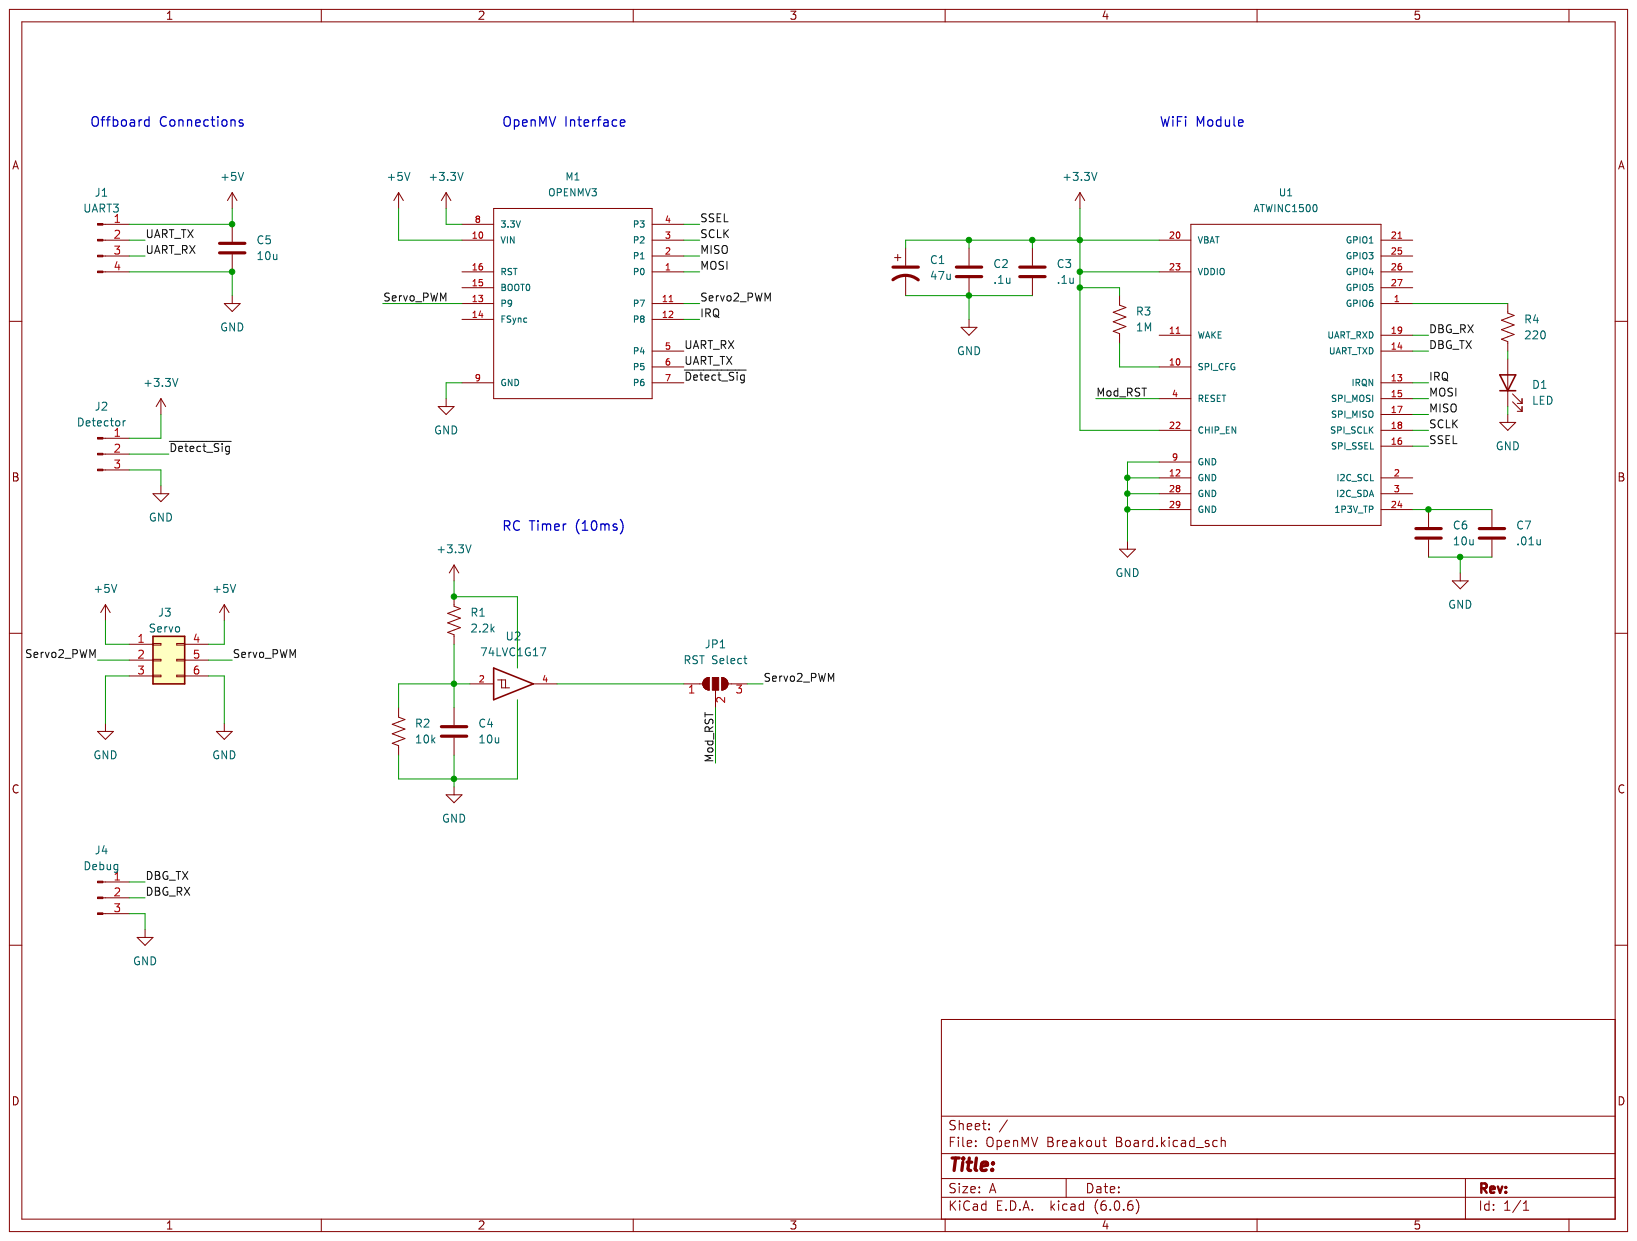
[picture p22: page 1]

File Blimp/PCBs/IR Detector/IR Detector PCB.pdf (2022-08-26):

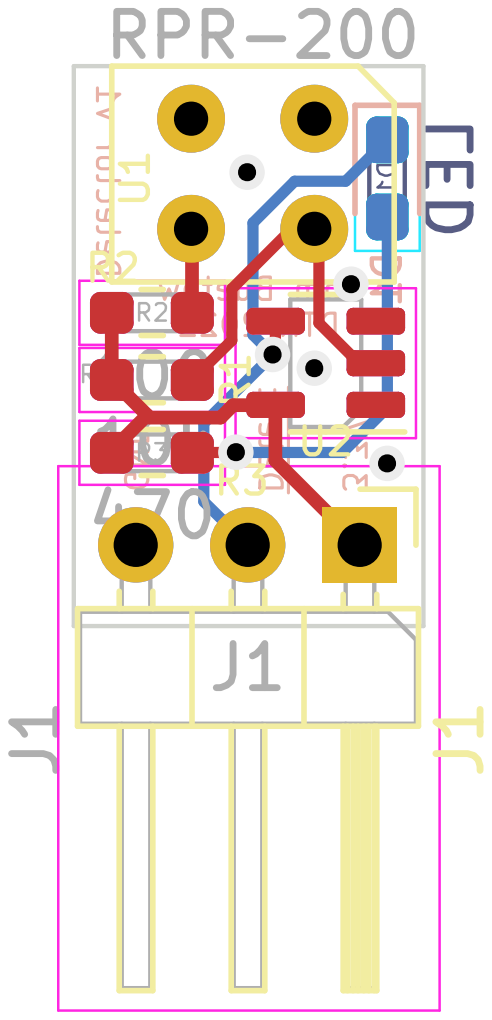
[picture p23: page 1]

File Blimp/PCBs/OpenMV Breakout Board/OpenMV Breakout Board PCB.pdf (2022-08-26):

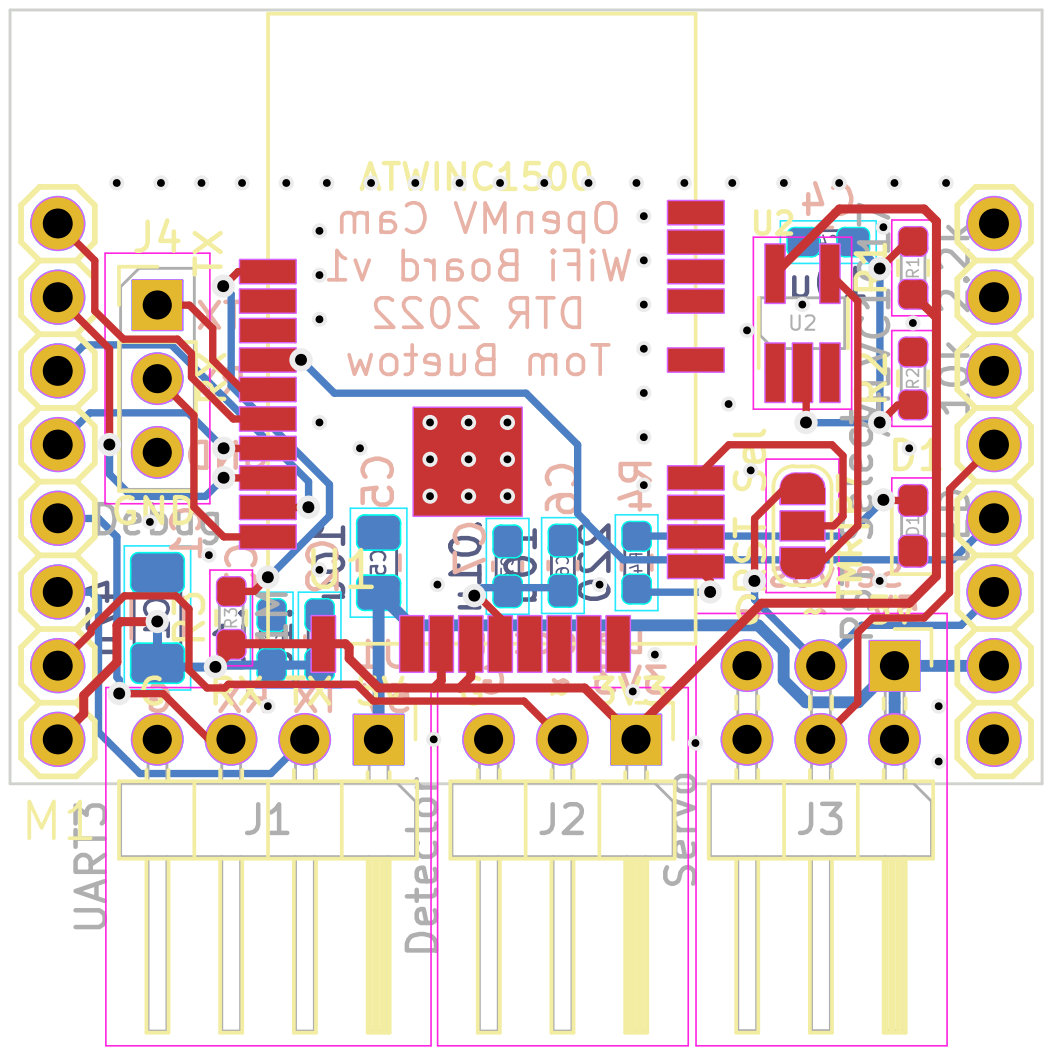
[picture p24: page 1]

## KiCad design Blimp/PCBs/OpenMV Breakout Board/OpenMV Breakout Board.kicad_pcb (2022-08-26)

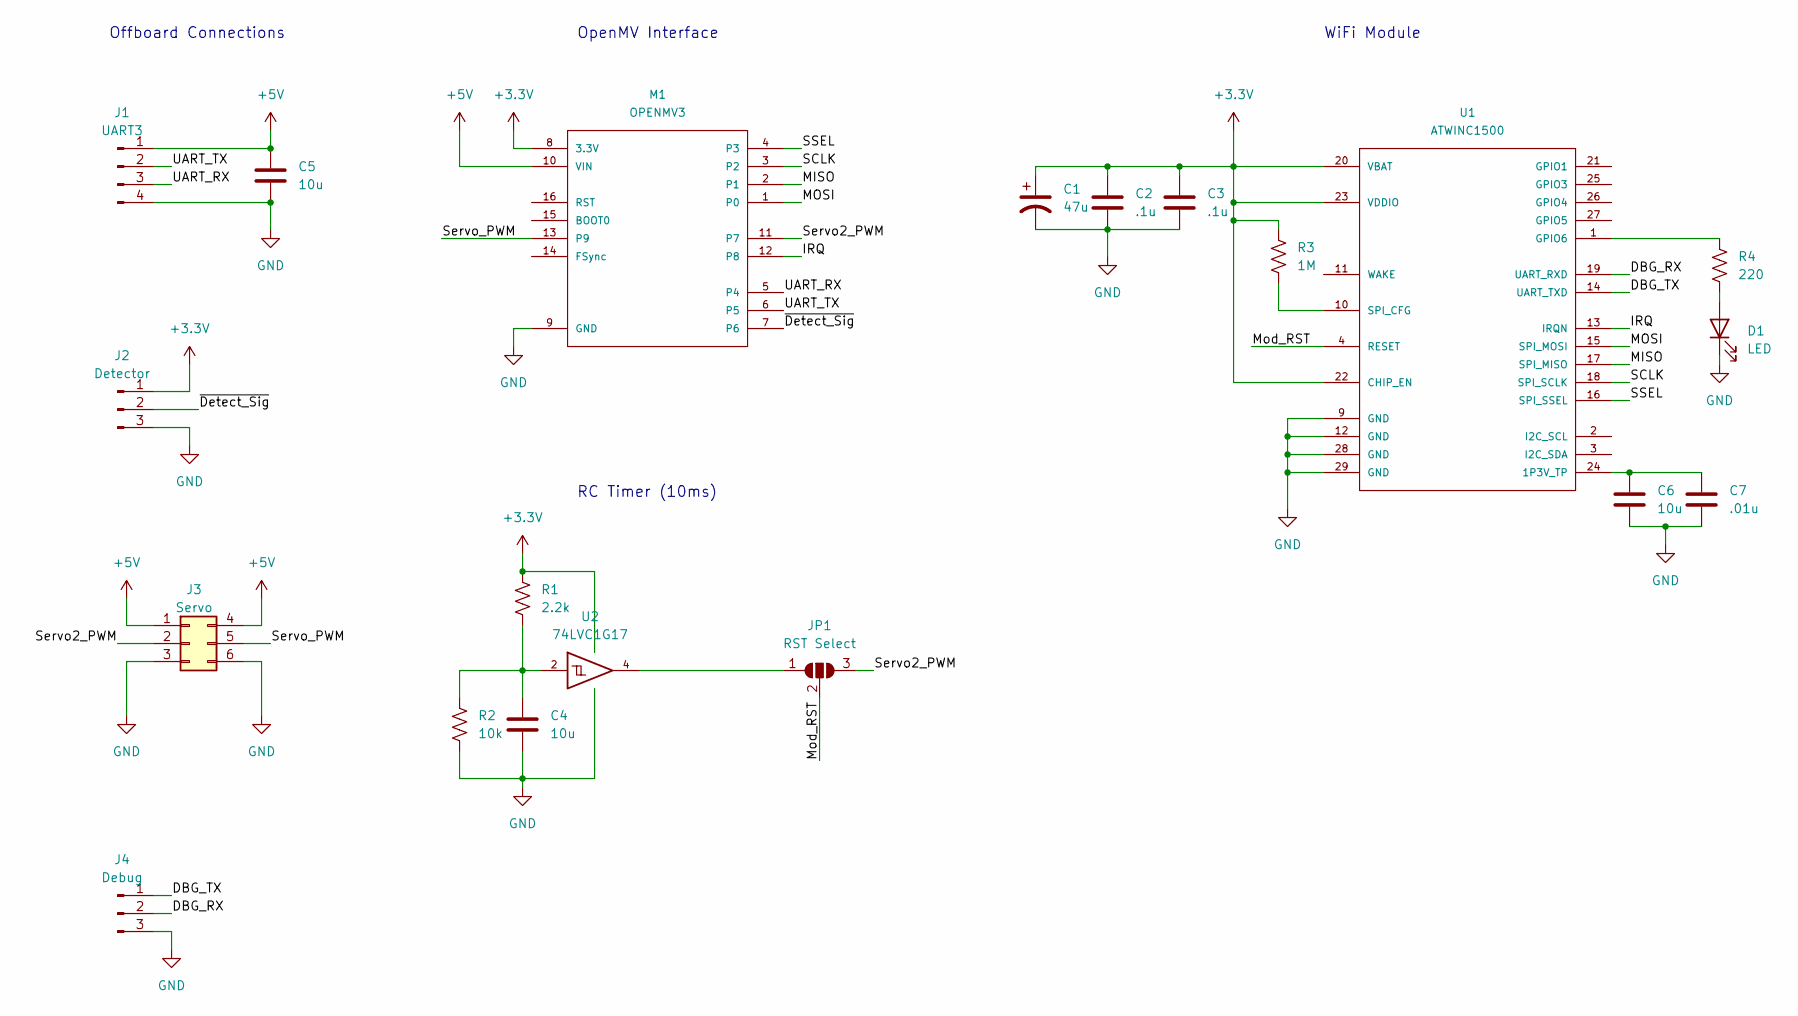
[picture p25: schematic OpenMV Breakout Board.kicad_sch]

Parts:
C1: 47u; C_1206_3216Metric_Pad1.33x1.80mm_HandSolder
C2, C3: .1u; C_0603_1608Metric_Pad1.08x0.95mm_HandSolder
C4, C6: 10u; C_0603_1608Metric_Pad1.08x0.95mm_HandSolder
C5: 10u; C_0805_2012Metric_Pad1.18x1.45mm_HandSolder
C7: .01u; C_0603_1608Metric_Pad1.08x0.95mm_HandSolder
D1: LED; LED_0603_1608Metric_Pad1.05x0.95mm_HandSolder
J1: UART3; PinHeader_1x04_P2.54mm_Horizontal
J2: Detector; PinHeader_1x03_P2.54mm_Horizontal
J3: Servo; PinHeader_2x03_P2.54mm_Horizontal
J4: Debug; PinHeader_1x03_P2.54mm_Vertical
JP1: RST Select; SolderJumper-3_P1.3mm_Open_RoundedPad1.0x1.5mm_NumberLabels
M1: OPENMV3
R1: 2.2k; R_0603_1608Metric_Pad0.98x0.95mm_HandSolder
R2: 10k; R_0603_1608Metric_Pad0.98x0.95mm_HandSolder
R3: 1M; R_0603_1608Metric_Pad0.98x0.95mm_HandSolder
R4: 220; R_0603_1608Metric_Pad0.98x0.95mm_HandSolder
U1: ATWINC1500
U2: 74LVC1G17; TSOT-23-5_HandSoldering

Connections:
+3.3V: C1.1, C2.1, C3.1, J2.1, M1.8 (3.3V), R1.1, R3.1, U1.20 (VBAT), U1.22 (CHIP_EN), U1.23 (VDDIO), U2.5 (VCC)
+5V: C5.1, J1.1, J3.1, J3.4, M1.10 (VIN)
/DBG_RX: J4.2, U1.19 (UART_RXD)
/DBG_TX: J4.1, U1.14 (UART_TXD)
/IRQ: M1.12 (P8), U1.13 (IRQN)
/MISO: M1.2 (P1), U1.17 (SPI_MISO)
/MOSI: M1.1 (P0), U1.15 (SPI_MOSI)
/Mod_RST: JP1.2 (C), U1.4 (RESET)
/SCLK: M1.3 (P2), U1.18 (SPI_SCLK)
/SSEL: M1.4 (P3), U1.16 (SPI_SSEL)
/Servo2_PWM: J3.2, JP1.3 (B), M1.11 (P7)
/Servo_PWM: J3.5, M1.13 (P9)
/UART_RX: J1.3, M1.5 (P4)
/UART_TX: J1.2, M1.6 (P5)
/~Detect_Sig: J2.2, M1.7 (P6)
GND: C1.2, C2.2, C3.2, C4.2, C5.2, C6.2, C7.2, D1.1 (K), J1.4, J2.3, J3.3, J3.6, J4.3, M1.9 (GND), R2.2, U1.9 (GND), U1.12 (GND), U1.28 (GND), U1.29 (GND), U2.3 (GND)
unnamed: C4.1, R1.2, R2.1, U2.2
unnamed: C6.1, C7.1, U1.24 (1P3V_TP)
unnamed: D1.2 (A), R4.2
unnamed: JP1.1 (A), U2.4
unnamed: R3.2, U1.10 (SPI_CFG)
unnamed: R4.1, U1.1 (GPIO6)

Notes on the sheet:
WiFi Module
Offboard Connections
RC Timer (10ms)
OpenMV Interface

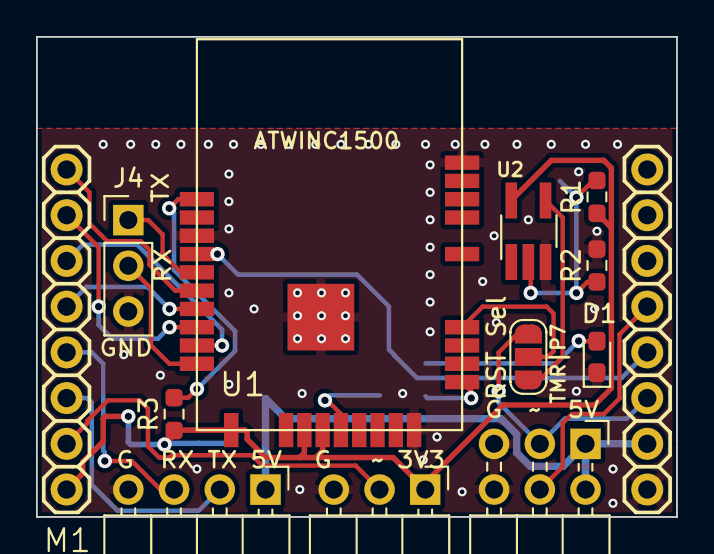
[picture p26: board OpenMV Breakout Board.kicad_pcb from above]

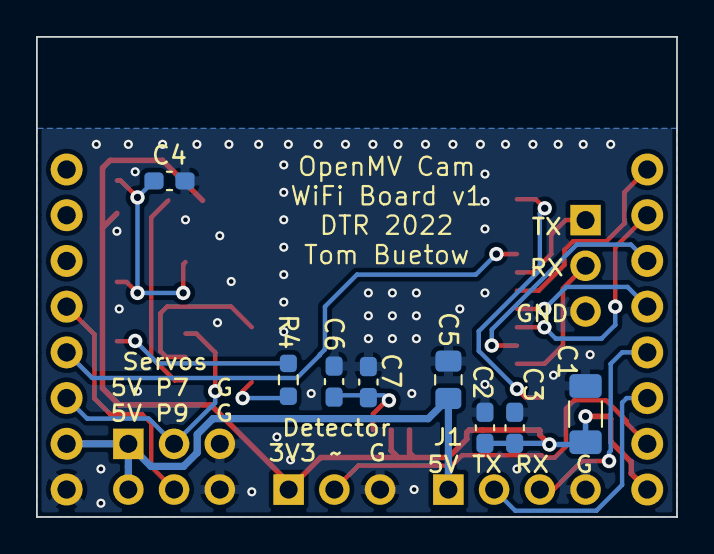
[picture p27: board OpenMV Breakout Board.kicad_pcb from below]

Board: 2 copper layers, 35.6 x 26.7 mm, 20 parts (8 on the bottom side), 22 nets.

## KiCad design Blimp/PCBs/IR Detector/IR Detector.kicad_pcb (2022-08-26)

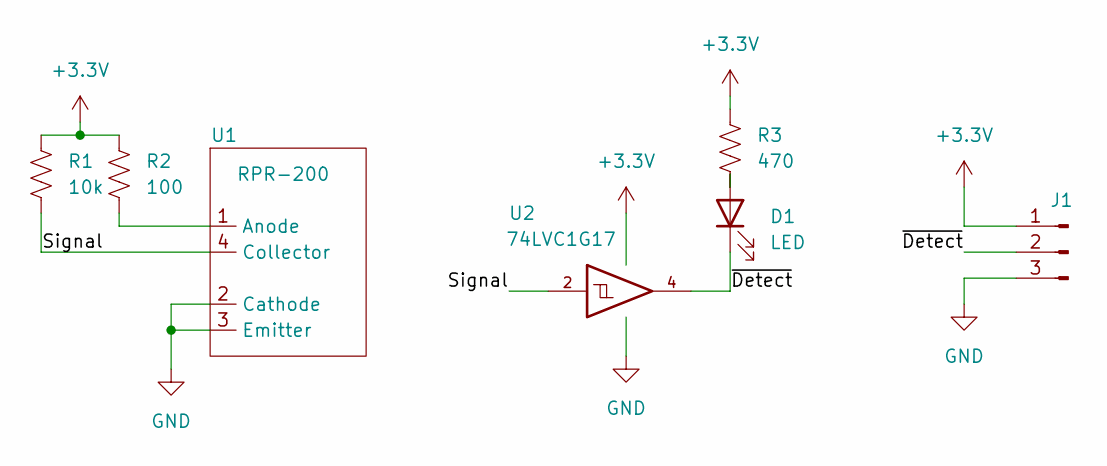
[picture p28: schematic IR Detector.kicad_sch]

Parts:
D1: LED; LED_0603_1608Metric_Pad1.05x0.95mm_HandSolder
J1: J1; PinHeader_1x03_P2.54mm_Horizontal
R1: 10k; R_0603_1608Metric_Pad0.98x0.95mm_HandSolder
R2: 100; R_0603_1608Metric_Pad0.98x0.95mm_HandSolder
R3: 470; R_0603_1608Metric_Pad0.98x0.95mm_HandSolder
U1: RPR-200
U2: 74LVC1G17; SOT-23-5

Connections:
+3.3V: J1.1, R1.1, R2.1, R3.1, U2.5 (VCC)
/Signal: R1.2, U1.4 (Collector), U2.2
/~Detect: D1.1 (K), J1.2, U2.4
GND: J1.3, U1.2 (Cathode), U1.3 (Emitter), U2.3 (GND)
unnamed: D1.2 (A), R3.2
unnamed: R2.2, U1.1 (Anode)

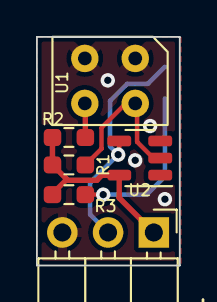
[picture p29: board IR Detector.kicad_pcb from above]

Board: 2 copper layers, 7.9 x 12.7 mm, 7 parts (1 on the bottom side), 6 nets.

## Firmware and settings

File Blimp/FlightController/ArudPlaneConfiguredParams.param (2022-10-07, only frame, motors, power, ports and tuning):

BATT_MONITOR,0
BATT2_MONITOR,0
BATT3_MONITOR,0
BATT4_MONITOR,0
BATT5_MONITOR,0
BATT6_MONITOR,0
BATT7_MONITOR,0
BATT8_MONITOR,0
BATT9_MONITOR,0
FLTMODE_CH,8
FLTMODE1,0
FLTMODE2,0
FLTMODE3,0
FLTMODE4,0
FLTMODE5,0
FLTMODE6,0
INS_GYRO_FILTER,20
INS_HNTCH_ENABLE,0
SERIAL0_BAUD,115
SERIAL0_PROTOCOL,2
SERIAL1_BAUD,115
SERIAL1_OPTIONS,0
SERIAL1_PROTOCOL,9
SERIAL2_BAUD,115
SERIAL2_OPTIONS,0
SERIAL2_PROTOCOL,1
SERIAL3_BAUD,38
SERIAL3_OPTIONS,0
SERIAL3_PROTOCOL,5
SERIAL4_BAUD,38
SERIAL4_OPTIONS,0
SERIAL4_PROTOCOL,5
SERIAL5_BAUD,921600
SERIAL5_OPTIONS,0
SERIAL5_PROTOCOL,2
SERIAL6_BAUD,57
SERIAL6_OPTIONS,0
SERIAL6_PROTOCOL,-1
SERVO1_FUNCTION,53
SERVO1_MAX,1900
SERVO1_MIN,1100
SERVO1_REVERSED,0
SERVO1_TRIM,1500
SERVO2_FUNCTION,54
SERVO2_MAX,1900
SERVO2_MIN,1100
SERVO2_REVERSED,0
SERVO2_TRIM,1500
SERVO3_FUNCTION,52
SERVO3_MAX,1900
SERVO3_MIN,1100
SERVO3_REVERSED,0
SERVO3_TRIM,1500
SERVO4_FUNCTION,51
SERVO4_MAX,1900
SERVO4_MIN,1100
SERVO4_REVERSED,0
SERVO4_TRIM,1500
SERVO5_FUNCTION,0
SERVO5_MAX,1900
SERVO5_MIN,1100
SERVO5_REVERSED,0
SERVO5_TRIM,1500
SERVO6_FUNCTION,0
SERVO6_MAX,1900
SERVO6_MIN,1100
SERVO6_REVERSED,0
SERVO6_TRIM,1500
SERVO7_FUNCTION,0
SERVO7_MAX,1900
SERVO7_MIN,1100
SERVO7_REVERSED,0
SERVO7_TRIM,1500
SERVO8_FUNCTION,0
SERVO8_MAX,1900
SERVO8_MIN,1100
SERVO8_REVERSED,0
SERVO8_TRIM,1500
SERVO9_FUNCTION,0
SERVO9_MAX,1900
SERVO9_MIN,1100
SERVO9_REVERSED,0
SERVO9_TRIM,1500

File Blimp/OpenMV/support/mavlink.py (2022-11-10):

import struct, time
import logger

UART_READ_SIZE = 256 #64, 128, 256

THROTTLE_SERVO = 1  
YAW_SERVO = 2
UP_SERVO = 3
MSG_RATE = 25000 #40Hz messaging rate
RCCH = 35
ATTITUDE = 30
SERVO = 36
LIDAR = 132
PRESSURE = 29
QUATERNION = 31
RAWIMU = 27

SUPPRESS_MSG = -1



class MavLink():
    '''Implements select Mavlink v1 messages to enable bydirectional communication between 
    OpenMV and Pixracer (ardupilot)'''
    def __init__(self,hw):
        self.hw = hw
        self._uart = hw.uart
        self.__ps = -1 #starting packet number
        self.ser_buf = bytearray()

        time.sleep(0.25) #Allow UART to initialize before sending messages MAYBE NOT NEEDED

     #   reject_msg = [74,65,1,42,227,22,253,125,27,24,241,0,146,2,165,163,168,233,116,172,193]
     #   for msg in reject_msg:
      #      self.send_set_msg_interval_cmd(msg,SUPPRESS_MSG)
       #     time.sleep(0.25)

        self.send_set_msg_interval_cmd(RCCH,MSG_RATE) #RC_Channels_Raw
        self.send_set_msg_interval_cmd(ATTITUDE,MSG_RATE) #Attitude
        self.send_set_msg_interval_cmd(SERVO,MSG_RATE) #Servo Channels
        self.send_set_msg_interval_cmd(LIDAR,MSG_RATE) #LIDAR
        self.send_set_msg_interval_cmd(QUATERNION,MSG_RATE) 
        self.send_set_msg_interval_cmd(PRESSURE,MSG_RATE) 
        #self.send_set_msg_interval_cmd(RAWIMU,MSG_RATE) 


    def __get_ps(self):
        '''update packet sequence number'''
        self.__ps += 1
        if self.__ps > 255:
            self.__ps = 0

        return self.__ps


    def __checksum(self,data, extra):
        '''Calculate checksum of packet
        https://github.com/mavlink/c_library_v1/blob/master/checksum.h'''
        output = 0xFFFF
        for i in range(len(data)):
            tmp = data[i] ^ (output & 0xFF)
            tmp = (tmp ^ (tmp << 4)) & 0xFF
            output = ((output >> 8) ^ (tmp << 8) ^ (tmp << 3) ^ (tmp >> 4)) & 0xFFFF
        tmp = extra ^ (output & 0xFF)
        tmp = (tmp ^ (tmp << 4)) & 0xFF
        output = ((output >> 8) ^ (tmp << 8) ^ (tmp << 3) ^ (tmp >> 4)) & 0xFFFF
        return output


    def __msg_frame(self,msg_id, extra_crc, payload, ps, sys_id=1, comp_id=1):
        '''builds serial mavlink packet with checksum'''
        payload_len = len(payload)
        msg = struct.pack("<BBBBB{}s".format(payload_len), #https://mavlink.io/en/guide/serialization.html#v1_packet_format
                            payload_len,
                            ps & 0xFF,
                            sys_id,
                            comp_id,
                            msg_id,
                            payload)

        return struct.pack("<B{}sH".format(5+payload_len),
                            0xFE,
                            msg,
                            self.__checksum(msg,extra_crc))


    def _build_msg_param_req_lst(self):
        '''Requests a list of all the available parameters and their current values
        https://github.com/mavlink/c_library_v1/blob/master/common/mavlink_msg_param_request_list.h'''
        system_id = 1 #1 is main flight controller
        component_id = 1 #not sure what "1" is, but hopefully it is the main component of the flight controller
        payload = struct.pack("<bb",system_id,component_id) #payload format from https://mavlink.io/en/messages/common.html#PARAM_REQUEST_LIST
  
        return self.__msg_frame(21,159,payload,self.__get_ps())


    def _build_msg_manual_control(self, x=0, #pitch (fwd/bk of right stick)
                                          y=0, #roll (left/right of right stick)
                                          z=0, #thrust (fwd/bk of left stick)
                                          r=0, #yaw (left/right of left stick)
                                          buttons=0): #8-bit bitfield
        '''NOTE: CURRENTLY NOTE IMPELEMENTED
        https://github.com/mavlink/c_library_v1/blob/master/common/mavlink_msg_manual_control.h'''
        target = 0 #target system to be controlled #TODO what does this mean?
        payload = struct.pack("<hhhhHB",x,y,z,r,buttons,target) 
     
        return self.__msg_frame(69,243,payload,self.__get_ps())



    def _build_msg_ch_overide(self, ch=(0,0,0,0,0,0,0,0)):
        '''NOTE: CURRENTLY NOTE IMPELEMENTED
        https://github.com/mavlink/c_library_v1/blob/master/common/mavlink_msg_rc_channels_override.h'''
        target_system = 1
        target_component = 1
        payload = struct.pack("<8HBB",ch[0],ch[1],ch[2],ch[3],ch[4],ch[5],ch[6],ch[7],
                                target_system,target_component)
 
        return self.__msg_frame(70,124,payload,self.__get_ps())


    def _build_msg_cmd_long(self,cmd,params=[float('NaN')]*7):
        '''Command Protocol message, mavlink returns Command ACK (#77) upon receipt of this message
        https://github.com/mavlink/c_library_v1/blob/master/common/mavlink_msg_command_long.h'''
        if len(params)<7:
            logger.log.verbose("ERROR: command_long message requires exactly 7 parameters, unused param locations should be filled with NaN.")
            return False
        target_system = 1
        target_component = 1 #TODO maybe "0"?
        confirm = 0 #TODO nonzero for retransmits
        payload = struct.pack("<7fHBBB",params[0],params[1],params[2],params[3],
                                        params[4],params[5],params[6],
                                        cmd,target_system,target_component,confirm)

        return self.__msg_frame(76,152,payload,self.__get_ps())


    def _build_msg_set_msg_int(self,msg_id,interval,target=0):
        '''Set params for mav_cmd_set_message_interval #511
        id = message number
        inter = interval in usec'''
        return [msg_id,interval,float('Nan'),float('NaN'),float('NaN'),float('NaN'),target]


    def _build_msg_cmd_req_msg(self,id):
        '''Functions similar to _build_msg_set_msg_int, but used for ONE SHOT messages
        Set params for mav_cmd_request_message #512'''
        return [id,float('Nan'),float('NaN'),float('NaN'),float('NaN'),float('NaN'),float('NaN')]


    def _build_frame_cmd_do_set_servo(self,servo_ch,value):
        '''Set params for mav_cmd_do_set_servo #183
        servo_ch= servo channel number
        value = PWM value (us)
        '''
        return [servo_ch,value,float('NaN'),float('NaN'),float('NaN'),float('NaN'),float('NaN')]

    def _build_frame_cmd_do_repeat_servo(self,servo_ch,value):
        '''Set params for mav_cmd_do_repeat_servo #184
        servo_ch= servo channel number
        value = PWM value (us)
        cycle_count = count
        cycle_time = time_in_seconds (some discussion that maybe this is really in ms)
        '''
        return [servo_ch,value,1,0.5,float('NaN'),float('NaN'),float('NaN')]


    def send_set_msg_interval_cmd(self,msg_id,interval):
        '''Send cmd message #511 to set desired publish rate of msg.
        msg_id = message type to be published
        interval = message interval in us'''
        cmd = self._build_msg_cmd_long(511,params=self._build_msg_set_msg_int(msg_id,interval,target=0))
        self._uart.write(cmd)


    def send_set_servo_cmd(self,servo,pwm):
        '''Send command messsage to set values of individual servos'''
        cmd = self._build_msg_cmd_long(183,params=self._build_frame_cmd_do_set_servo(servo,pwm))
        #cmd = self._build_msg_cmd_long(184,params=self._build_frame_cmd_do_repeat_servo(servo,pwm))
        self._uart.write(cmd)
        logger.log.verbose('Sent motor command -- SERVO:' + str(servo) + ' PWM: ' + str(pwm))


    def __cntl_to_pwm(self,value):
        '''Helper to convert -1 -- 1 values of controls to PWM values (us)'''
        return(400*value+1500)


    def setControls(self,controls):
        '''Send corresponding mavlink message to set servo values based on current settings of controls object'''

        self.send_set_servo_cmd(YAW_SERVO,self.__cntl_to_pwm(controls.yaw)) #YAW Servo Channel 2
        self.send_set_servo_cmd(THROTTLE_SERVO,self.__cntl_to_pwm(controls.throttle)) #THROTTLE Servo Channel 1
        self.send_set_servo_cmd(UP_SERVO,self.__cntl_to_pwm(controls.up)) #UP Servo Channel 3


    def _read_uart(self): #TODO Run tests to see if buffer is emptying out fast enough
        '''Read contents of serial buffer and parse messages
        Parse a message:
            msg[0] = start byte (254)
            msg[1] = message payload length (not including header or checksum
            msg[2] = sequence number (0-255)
            msg[3] = systems id (should always be 1)
            msg[4] = component id (usually 1)
            msg[5] = message type 
            msg[6:6+n] = payload n = message payload length
            msg[6+n:6+n+3] = checksum'''
        #logger.log.verbose('bytes in uart: ' + str(self._uart.any()))
        result = self._uart.read(UART_READ_SIZE)
       
        if result == None:
            return None
        else:
            r_pntr = 0 #read_pointer - tracks read position in message buffer
            msg_list = [] #stores all parsed messages
            while r_pntr < len(result):
                if result[r_pntr] == 254:
                    try: #Message found
                        msg_type = result[r_pntr+5] #Message Id
                        full_msg = result[r_pntr+1:r_pntr+6+result[r_pntr+1]]
                        crc = result[r_pntr+6+result[r_pntr+1]:r_pntr+6+result[r_pntr+1]+2]
                        payload = result[r_pntr+6:r_pntr+6+result[r_pntr+1]] #Msg payload in bytes
                        msg = (result[r_pntr+5],payload)
                        if self.__decode_checksum(msg_type,full_msg,crc): #is checksum valid
                            msg_list.append(msg)
                        r_pntr += 6+result[r_pntr+1]+2 #advance read pointer to next message
                    except IndexError:
                        return msg_list
                else:
                    r_pntr += 1
            return msg_list


    def __decode_checksum(self,msg_id,msg,checksum):
        '''check the checksum from incoming message'''
        if msg_id == RCCH:
            extra_crc = 244
        elif msg_id == ATTITUDE:
            extra_crc = 39
        elif msg_id == SERVO:
            extra_crc = 222
        elif msg_id == LIDAR:
            extra_crc = 85
        elif msg_id == PRESSURE:
            extra_crc = 115
        elif msg_id == QUATERNION:
            extra_crc = 246
        else:
            return True

        computed_checksum = self.__checksum(msg,extra_crc)
        try:
            rcvd_checksum = struct.unpack("<H",checksum)[0]
           # print("RCVD CHECKSUM: ", cs)
            if computed_checksum == rcvd_checksum: #good CRC
                return True
            
            else: #bad CRC
                return False
        except ValueError: #msg cutoff before crc was read
            return False


    def __parse_lidar_msg(self,msg):
        '''https://github.com/mavlink/c_library_v1/blob/master/common/mavlink_msg_distance_sensor.h
           https://mavlink.io/en/messages/common.html#DISTANCE_SENSOR
           Byte order:
            char buf[MAVLINK_MSG_ID_DISTANCE_SENSOR_LEN];
            _mav_put_uint32_t(buf, 0, time_boot_ms);
            _mav_put_uint16_t(buf, 4, min_distance);
            _mav_put_uint16_t(buf, 6, max_distance);
            _mav_put_uint16_t(buf, 8, current_distance);
            _mav_put_uint8_t(buf, 10, type);
            _mav_put_uint8_t(buf, 11, id);
            _mav_put_uint8_t(buf, 12, orientation);
            _mav_put_uint8_t(buf, 13, covariance);
        '''
        try:
            return struct.unpack('<1H',msg[8:10])[0] #current_distance
  
        except ValueError:
            return None


    def __parse_attitude_msg(self,msg):
        '''https://github.com/mavlink/c_library_v1/blob/master/common/mavlink_msg_attitude.h
           https://mavlink.io/en/messages/common.html#ATTITUDE
           Byte order: 
            char buf[MAVLINK_MSG_ID_ATTITUDE_LEN];
            _mav_put_uint32_t(buf, 0, time_boot_ms);
            _mav_put_float(buf, 4, roll);
            _mav_put_float(buf, 8, pitch);
            _mav_put_float(buf, 12, yaw);
            _mav_put_float(buf, 16, rollspeed);
            _mav_put_float(buf, 20, pitchspeed);
            _mav_put_float(buf, 24, yawspeed);
        '''
        try:
            att_tup = struct.unpack('<6f',msg[4:28]) #(roll,pitch,yaw,rollspeed,pitchspeed,yawspeed)
            return {'roll': att_tup[0],'pitch':att_tup[1],'yaw':att_tup[2],
                    'roll_speed':att_tup[3],'pitch_speed':att_tup[4],'yaw_speed':att_tup[5]}
            #return (struct.unpack('<6f',msg[4:28])) 
        except ValueError:
            return None


    def __parse_rc_ch_msg(self,msg):
        '''https://github.com/mavlink/c_library_v1/blob/master/common/mavlink_msg_rc_channels_raw.h
           https://mavlink.io/en/messages/common.html#RC_CHANNELS_RAW
           Byte Order:
            char buf[MAVLINK_MSG_ID_RC_CHANNELS_RAW_LEN];
            _mav_put_uint32_t(buf, 0, time_boot_ms);
            _mav_put_uint16_t(buf, 4, chan1_raw);
            _mav_put_uint16_t(buf, 6, chan2_raw);
            _mav_put_uint16_t(buf, 8, chan3_raw);
            _mav_put_uint16_t(buf, 10, chan4_raw);
            _mav_put_uint16_t(buf, 12, chan5_raw);
            _mav_put_uint16_t(buf, 14, chan6_raw);
            _mav_put_uint16_t(buf, 16, chan7_raw);
            _mav_put_uint16_t(buf, 18, chan8_raw);
            _mav_put_uint8_t(buf, 20, port);
            _mav_put_uint8_t(buf, 21, rssi);
        '''
        try:
            rc_tup = struct.unpack('<8H',msg[4:20]) #(roll,pitch,yaw,rollspeed,pitchspeed,yawspeed)
            return {'ch1': rc_tup[0],'ch2':rc_tup[1],'ch3':rc_tup[2],
                    'ch4':rc_tup[3],'ch5':rc_tup[4],'ch6':rc_tup[5],
                    'ch7':rc_tup[6],'ch8':rc_tup[7]}
            #return (struct.unpack('<8H',msg[4:20]))
        except ValueError:
            return None


    def __parse_servo_output_msg(self,msg):
        '''https://github.com/mavlink/c_library_v1/blob/master/common/mavlink_msg_servo_output_raw.h
           https://mavlink.io/en/messages/common.html#SERVO_OUTPUT_RAW
           Byte order:
            _mav_put_uint32_t(buf, 0, time_usec);
            _mav_put_uint16_t(buf, 4, servo1_raw);
            _mav_put_uint16_t(buf, 6, servo2_raw);
            _mav_put_uint16_t(buf, 8, servo3_raw);
            _mav_put_uint16_t(buf, 10, servo4_raw);
            _mav_put_uint16_t(buf, 12, servo5_raw);
            _mav_put_uint16_t(buf, 14, servo6_raw);
            _mav_put_uint16_t(buf, 16, servo7_raw);
            _mav_put_uint16_t(buf, 18, servo8_raw);
            _mav_put_uint8_t(buf, 20, port);'''
        try:
            sv_tup = struct.unpack('<8H',msg[4:20])
            return {'servo1': sv_tup[0],'servo2':sv_tup[1],'servo3':sv_tup[2],
                    'servo4':sv_tup[3],'servo5':sv_tup[4],'servo6':sv_tup[5],
                    'servo7':sv_tup[6],'servo8':sv_tup[7]}
        except ValueError:
            return None


    def __parse_pressure_msg(self,msg):
        '''https://github.com/mavlink/c_library_v1/blob/master/common/mavlink_msg_scaled_pressure.h
        https://mavlink.io/en/messages/common.html#SCALED_PRESSURE
        Byte order:
         _mav_put_uint32_t(buf, 0, time_boot_ms);
         _mav_put_float(buf, 4, press_abs);
         _mav_put_float(buf, 8, press_diff);
         _mav_put_int16_t(buf, 12, temperature);
         '''
        try:
            pres_tup = struct.unpack('<2fh',msg[4:14]) #(roll,pitch,yaw,rollspeed,pitchspeed,yawspeed)
            return {'press_abs': pres_tup[0],'press_diff':pres_tup[1],'temp':pres_tup[2]}
        except ValueError:
            return None


    def __parse_quarternion_msg(self,msg):
        '''https://github.com/mavlink/c_library_v1/blob/master/common/mavlink_msg_scaled_pressure.h
        https://mavlink.io/en/messages/common.html#ATTITUDE_QUATERNION
        Byte order:
         _mav_put_uint32_t(buf, 0, time_boot_ms);
         _mav_put_float(buf, 4, q1);
         _mav_put_float(buf, 8, q2);
         _mav_put_float(buf, 12, q3);
         _mav_put_float(buf, 16, q4);
         _mav_put_float(buf, 20, rollspeed);
         _mav_put_float(buf, 24, pitchspeed);
         _mav_put_float(buf, 28, yawspeed);
         '''
        try:
            att_tup = struct.unpack('<7f',msg[4:32]) #(q1,q2,q3,q4,rollspeed,pitchspeed,yawspeed)
            return {'q1': att_tup[0],'q2':att_tup[1],'q3':att_tup[2], 'q4':att_tup[3],
                    'roll_speed':att_tup[4],'pitch_speed':att_tup[5],'yaw_speed':att_tup[6]}
        except ValueError:
            return None


    def getSensors(self):
        '''Returns dict where key = Sensor_type, value = most recent value received via mavlink'''
        start = time.time_ns()
        msg_list = self._read_uart()     
        uartReadTime = (time.time_ns() - start)/1e9
        logger.log.verbose('mavlink uart read: ' + str(uartReadTime))
        


        if(msg_list == None):
            #logger.log.warning(">>>>>>>>>>>>>>>>>>") 
            #logger.log.warning("MAVLINK LINK FAIL")
            #logger.log.warning(">>>>>>>>>>>>>>>>>>") 
            self.hw.systemFail()

        sensors = {'Attitude': None, 'RCCH': None, 'Servo': None, 'Lidar': None, 'Pressure': None}
        
        if msg_list != None:
            for msg in msg_list:
                if msg[0] == ATTITUDE:
                    result = self.__parse_attitude_msg(msg[1])
                    if result != None:
                        sensors['Attitude'] = result
                        logger.log.info("mavlink 1 - new attitude data!")
                elif msg[0] == RCCH:
                    result = self.__parse_rc_ch_msg(msg[1])
                    if result != None:
                        sensors['RCCH'] = result
                        logger.log.info("mavlink 2 - new rcch data!")
                elif msg[0] == SERVO:
                    result = self.__parse_servo_output_msg(msg[1])
                    if result != None:
                        sensors['Servo'] = result
                        logger.log.info("mavlink 3 - new servo data!")
                elif msg[0] == LIDAR:
                    result = self.__parse_lidar_msg(msg[1])               
                    if result != None:                                               
                        sensors['Lidar'] = result
                        logger.log.info("mavlink 4 - new lidar data!")
                elif msg[0] == PRESSURE:
                    result = self.__parse_pressure_msg(msg[1])               
                    if result != None:                                               
                        sensors['Pressure'] = result
                        logger.log.info("mavlink 5 - new lidar data!")
                elif msg[0] == QUATERNION:
                    result = self.__parse_quarternion_msg(msg[1])               
                    if result != None:                                               
                        sensors['Quarternion'] = result
                        logger.log.info("mavlink 6 - new quaternion data!")

        return sensors #Any sensor that is not updated will return 'None'


#if __name__ == "__main__":
#     import pyb
#     class hardware():
#         def __init__(self):
#             UART_BAUDRATE = 115200
#             UART_TIMEOUT = 50
#             self.uart = pyb.UART(3)
#             self.uart.init(UART_BAUDRATE, timeout=UART_TIMEOUT, bits=8, parity=None, stop=1, flow=0, read_buf_len=64)
#         def systemFail(self):
#             pass
#     hw = hardware()
#     mvlink = MavLink(hw)
#     mn = 1
#     while True:
#        result = mvlink.getSensors()
#        #print(result)
#        mn += 1
#        time.sleep(0.5)
#        print(result)
#     #logger.log.verbose(result)

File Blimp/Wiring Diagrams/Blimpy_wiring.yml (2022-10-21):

#DTR Blimp Wiring diagram
#Wirviz 0.3.2 Specification https://github.com/formatc1702/WireViz

connectors:
#Pixracer
  Pixracer-Telem1: &PX_GH6_template
    pinlabels: [5V,TX,RX,CTS,RTS,GND]
    type: JST-GH_1.25
    subtype: female
    image:
      src: JST-GH Pin ID.png
      width: 200
  Pixracer-Telem2:
    <<: *PX_GH6_template
  Pixracer-PWR:
    <<: *PX_GH6_template
    pinlabels: [5V,5V,Csen,Vsen,GND,GND]
  Pixracer-RC:
    <<: *PX_GH6_template
    pinlabels: [5V,RCin,RSSI,3.3V,GND]
  Pixracer-Servos:
    pinlabels: [ch1,ch2,ch3,ch4,ch5,ch6]
    type: 0.1" header
    subtype: female
#RC Receiver
  RC_Receiver: &DP_SERVO_template
    pinlabels: [PWM,5V,GND]
    type: 0.1" header
    subtype: female
#OpenMV Hat
  OpenMV_Hat-Serial:
    <<: *DP_SERVO_template
    pinlabels: [5V,TXD,RXD,GND]
  OpenMV_Hat-Detector:
    <<: *DP_SERVO_template
    pinlabels: [3.3V,signal,GND]
  OpenMV_Hat-Servo1 - Top:
    <<: *DP_SERVO_template
    pinlabels: [5V,PWM,GND]
  OpenMV_Hat-Servo3 - Bottom:
    <<: *DP_SERVO_template
    pinlabels: [5V,PWM,GND]
#Sensors
  LIDAR-Serial:
    <<: *PX_GH6_template
    pinlabels: [TXD,RXD,5V,GND]
    notes: |
      Manufacturer documentation
      pin numbers are reversed.
      Pin #s here are correct.
  IR-Detector:
    <<: *DP_SERVO_template
    pinlabels: [3.3V,signal,GND]
#Battery and regulator
  5VRegulator:
    pinlabels: [Vin,GND,Vout]
    type: solder pad
  Battery: &Batt_PH_M_template
    pinlabels: [Vbatt,GND]
    type: JST-PH 2.0
    subtype: male
    image:
      src: JST-PH 2.0 Pin ID.png
      width: 200
  Battery-Reg: &Batt_PH_F_template
    <<: *Batt_PH_M_template
    subtype: female
    image:
      src: JST-PH 2.0 Female Pin ID.png
      width: 200
    notes: connects to soldered on JST-PH lead
  Reg-Power:
    <<: *Batt_PH_M_template
#Solder end
  solder:
    style: simple
    type: solder lead
    autogenerate: true

#ESCs and servos
  Lift ESC Signal:
    <<: *DP_SERVO_template
  Yaw ESC Signal:
    <<: *DP_SERVO_template
  Thrust ESC Signal:
    <<: *DP_SERVO_template
  Lift ESC Power:
    <<: *Batt_PH_F_template
  Yaw and Thrust ESC Power:
    <<: *Batt_PH_F_template
  Catch Servo:
    <<: *DP_SERVO_template
    pinlabels: [GND,5V,PWM]
    type: JST 1.25
    subtype: male
    image:
      src: JST 1.25 3 Pos Pin ID.png
      width: 200
    notes: Ignore cable colors in image.
  Rear ESC Power:
    <<: *Batt_PH_M_template
  Mid ESC Power: 
    <<: *Batt_PH_M_template

cables:
# Power distribution cables
  # Regulator Battery Cable:
  #   wirecount: 2
  #   length: 6 in
  #   gauge: 22 awg
  #   colors: [RD, BK]
  Mid ESC Power Cable:
    wirecount: 2
    gauge: 22 awg
    length: 6 in
    colors: [RD,BK]
  Rear ESC Power Cable:
    wirecount: 2
    gauge: 22 awg
    length: 7 in
    colors: [RD,BK]
  Regulator to Battery Cable:
    wirecount: 2
    gauge: 22 awg
    length: 7 in 
    colors: [RD,BK]
  Battery Distribution Cable 1:
    wirecount: 2
    gauge: 22 awg
    length: 8 in
    colors: [RD, BK]
  Battery Distribution Cable 2:
    wirecount: 2
    gauge: 22 awg
    length: 11 in
    colors: [RD, BK]
  Regulator 5V to Pixracer Cable:
    wirecount: 2
    gauge: 22 awg
    length: 6 in
    colors: [RD,BK]
# Servo cables
  Lift ESC Signal Cable:
    wirecount: 1
    gauge: 28 awg
    length: 6 in
    colors: [BU]
  Yaw ESC Signal Cable:
    wirecount: 1
    gauge: 28 awg
    length: 21 in
    colors: [GN]
  Thrust ESC Signal Cable:
    wirecount: 1
    gauge: 28 awg
    length: 22 in
    colors: [YE]
  CatchServoCable:
    wirecount: 3
    gauge: 28 awg
    length: 36 in
    colors: [RD,YE,BK]
# Sensor/Peripheral cables
  RCCable:
    wirecount: 3
    gauge: 28 awg
    length: 6 in
    colors: [BK,YE,RD]
  LIDARCable:
    wirecount: 4
    gauge: 28 awg
    length: 6 in
    colors: [RD,WH,BU,BK]
  PixOpenMVCable:
    wirecount: 4
    gauge: 22/28 awg
    length: 28 in
    colors: [RD,WH,BU,BK]
  DetectorCable:
    wirecount: 3
    gauge: 28 awg
    length: 24 in
    colors: [RD,GN,BK]
# #ESC/Reg power cables
#   Lift ESC Power Cable: &ESC_cable_template
#     wirecount: 2
#     gauge: 22 awg
#     length: 6 in
#     colors: [RD, BK]
#   Yaw and Thrust ESC Power Cable:
#     <<: *ESC_cable_template
#   Thrust ESC Power Cable:
#     <<: *ESC_cable_template
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

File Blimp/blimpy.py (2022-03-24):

import evdev
from evdev import InputDevice, categorize, ecodes 
import os
import sys
from time import sleep, time
from gpiozero import Servo, Motor, DigitalOutputDevice
from gpiozero.pins.pigpio import PiGPIOFactory
from attrdict import AttrDict
from collections import namedtuple
import numpy as np
import cv2
from simple_pid import PID
import board
import busio
#import adafruit_bno055 NO LONGER USED
import adafruit_tfmini
import serial
import threading
from flask import Flask, send_file
from subprocess import check_output
from gpiozero.pins.pigpio import PiGPIOFactory
import RPi.GPIO as GPIO

sys.path.append('/home/pi/dtr/bno055-python-i2c')
from BNO055 import BNO055

#MIN-MAX Settings for PWM control of ESCs and Servo
MIN_PULSE = 0.001148 #configurable using BLHeli_S ESC firmware uploader
MAX_PULSE = 0.001832
MAX_SERVO = 0.00217 #servo max/min found by trial and error
MIN_SERVO = 0.00052


#evdev mappings (change these to change controller configuration)
ps3 = AttrDict({'name': 'PLAYSTATION(R)3',
                'yaw': 'ABS_Z', 
                'thrust':'ABS_RX', 
                'up':'BTN_BASE4', 
                'down':'BTN_BASE3',
                'forward':'BTN_TOP2', 
                'backward':'BTN_BASE', 
                'left':'BTN_BASE2',
                'right':'BTN_PINKIE', 
                'deadman':'BTN_DEAD',
                'start':'BTN_TOP',
                'ball_captured': 'BTN_JOYSTICK',
                'trap': 'BTN_BASE6'}) #THESE MAPPINGS ARE FOR SONY BRAND PS3 Controller

#State definitions defined by self.state: 
#'in_position','target_located','target_inrange','target_captured','goal_located','goal_inrange', goal_oriented'
#self.state is compared to STATE to determine which state we are in.
STATE = AttrDict({      'READY':(False,False,False,False,False,False,False),
             'SEARCHING_TARGET':(True, False,False,False,False,False,False),
             'MOVING_TO_TARGET':(True, True, False,False,False,False,False),
             'CAPTURING_TARGET':(True, True, True, False,False,False,False),
               'SEARCHING_GOAL':(True, True, True, True, False,False,False),
               'MOVING_TO_GOAL':(True, True, True, True, True, False,False),
            'ORIENTING_TO_GOAL':(True, True, True, True, True, True, False),
                 'SCORING_GOAL':(True, True, True, True, True, True, True )})


class Blimpy():
    def __init__(self, g_color,  #goal color, either orange or yellow depending on which side we are assigned 
                    controller_map=ps3, #Need to add new controller map for evdev if non-PS3 controller used
                    allow_manual = True, #if only using autonomous control set to False (won't block waiting for controller)
                    pic_server = True): #Enables flask server to serve images from main camera
        '''Requires Goal color either "yellow" or "orange" 
        detect functions modify blimpy state vector
        perform functions modify action vector (except for perform_action)'''
        self.exiting = False

        self.loop_time = time()

        self.action = AttrDict({'yaw':0, #Action values provided by manual or autonomous controller
                                'thrust':0,
                                'altitude':0})

        #Setup motor signals for ESC control
        self.thrust_motor =  Servo(7, min_pulse_width=MIN_PULSE, max_pulse_width=MAX_PULSE, pin_factory=PiGPIOFactory())
        self.altitude_fwd =  Servo(12,min_pulse_width=MIN_PULSE, max_pulse_width=MAX_PULSE, pin_factory=PiGPIOFactory())
        self.altitude_rear = Servo(16,min_pulse_width=MIN_PULSE, max_pulse_width=MAX_PULSE, pin_factory=PiGPIOFactory())
        self.yaw_motor =     Servo(20,min_pulse_width=MIN_PULSE, max_pulse_width=MAX_PULSE, pin_factory=PiGPIOFactory())
        self.yaw_servo =     Servo(21,min_pulse_width=MIN_SERVO, max_pulse_width=MAX_SERVO, pin_factory=PiGPIOFactory())

        #self.ready = DigitalOutputDevice(X, initial_value=False) #Allows LED to show when in autonomous mode
        #self.door = Servo(XX, pin_factory=PiGPIOFactory()) #TODO set pin for capture door servo

        #Manual Control settings
        self.manual = controller_map
        self.manual_en = False #enable with dead man switch
        self.joystick = None #joystick object from evdev
        joystick_th = threading.Thread(target=self.joystick_monitor) #starts a thread to constantly read joystick

        #State dictionary
        self.state = AttrDict({'in_position': False, 
                                'target_located': False,
                                'target_inrange': False,
                                'target_captured': False,
                                'goal_located': False,
                                'goal_inrange': False,
                                'goal_oriented': False})
        
        if allow_manual: 
            self.connect_controller()
            joystick_th.start()
        else: #if no controller used assume autonomy starts immediately
            self.state.in_position = True

        #for trap door
        #TODO Add setup stuff for door servo using Servo function
        self.trap_closed = False

        #Camera Settings - using on-board ArduCam 
        self.video = cv2.VideoCapture(0)
        #Mask - Lower and Upper for [Hue, Staturation, Value] 
        #NOTE original green mask was [30,100,50]-[60,255,255]
        self.target_mask = np.array([[50,100,130],[70,255,255]],dtype='uint8') #mask for ball
        if g_color == 'yellow': 
            self.goal_mask = np.array([[25,100,120],[50,255,140]],dtype='uint8') #mask for yellow goal
        elif g_color == 'orange':
            self.goal_mask = np.array([[5,75,120],[20,255,255]],dtype='uint8') #mask for orange goal
        else:
            print("Goal color must be 'yellow' or 'orange'!")
            self.exiting = True
            sys.exit() 
        self.g_color = g_color
        self.current_mask = None #mask of current object of interest
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

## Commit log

2022-03-24 initial commit from other project
    [Motor Mount (newest) v4.stl, Parts_List.xlsx, PiZero_ESC_pin_diagram.xlsx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]
2022-05-19 ground control initial commit. server to receive messages w/ js test code works. micropython code ready to test with openMV camera once the wifi module is here. urequests library appears to work, but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
2022-05-20 First pass at configured params for ArduPilot code running on Pixracer
    [ArudPlaneConfiguredParams.param]
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2022-05-20 Ardupilot working with 3D motor control and differential thrust on ch 1, 2
    [ArduCopterConfiguredParams_forESCFlashing.param, ArudPlaneDefaultParams.param]
2022-05-23 UI initial commit - simply shows last heartbeat of blimp connection to ground station
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2022-05-23 brief reorg per quick code discusion
    [Motor Mount (newest) v4.stl, Servo Mount (Newest) v3.stl, big_servo_mount.stl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]
2022-05-27 dtr: basic main function working. added upload to mv camera and changed folder structure with main.py and support file folder
2022-05-27 fixed path issue with sending message to ground server
    [groundStation.py]
2022-06-10 fixed mavlink messages structure
    [copySupportFilesToCamera.py]
2022-08-05 Add openMV mount step and mesh files
    [openMV Mount v2.step, openMV Mount v2.stl]
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2022-08-05 updated arduplane config for 3 motor control
    [ArudPlaneConfiguredParams.param]
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2022-08-11 Catcher frame to balloon mount 3D files
    [Catcher Mount v1.step, Catcher Mount v1.stl]
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2022-08-12 blimp - main file runs again with open mv camera after unit test file path fixes.
    [dataClasses.py, groundStation.py, main.py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]
2022-08-12 fixed IR sensor. wifi module must be initialized first
    [main.py]
2022-08-12 system works now getting maneuver from db. responds correctly to sensor.
    [actionEngine.py, dataClasses.py, groundStation.py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]
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2022-08-12 OpenMV Cam breakout board as ordered 8/12/22
    [OpenMV Breakout Board.kicad_pcb, OpenMV Breakout Board.kicad_sch]
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2022-08-13 IR Detector board
    [IR Detector.kicad_pcb, IR Detector.kicad_sch]
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2022-08-20 Initial draft of wiring diagram for full blimp
    [Blimp_wireviz.bom.tsv]
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2022-08-21 Updates to OpenMV hat to make pin labels more legible on PCB. Change schematic to be A paper sized for printing, reorg for readability
    [OpenMV Breakout Board.kicad_pcb, OpenMV Breakout Board.kicad_sch]
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2022-08-21 IR Detector schematic change paper to A size. Add PDFs of schematics and PCBs for IR Detector and OpenMV Hat
    [IR Detector.kicad_pcb, IR Detector.kicad_sch]
2022-08-21 additional labels on pcb for servos
    [OpenMV Breakout Board.kicad_pcb]
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2022-08-22 refactor: runs now without error. need to allow it to talk to server via ethernet instead of wifi module when running in unit test mode.
    [actionEngine.py, comms.py, flightActions.py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]
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2022-08-30 Wiring harness includes lengths based on preliminary measurements
    [Blimp_wireviz.bom.tsv]
2022-08-31 Add hardware layout diagram with names matched to wiring diagram Rename Blimp_wireviz to Blimpy_wiring for project name consistency
    [Blimp_wireviz.bom.tsv, Blimpy_wiring.bom.tsv]
2022-08-31 Moved IR Detector and OpenMV Breakout folders from Blimp/ to Blimp/PCBs
    [IR Detector.kicad_pcb, IR Detector.kicad_sch, OpenMV Breakout Board.kicad_pcb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]
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2022-09-02 initialization script works with leds. purple for startup, green for running connected to server, yelowish for not connected to server, red for fail.
    [hardware.py, hardwareMock.py, main.py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]
2022-09-02 Add Fusion archive files for all my 3D models
    [Catcher Mount v1.f3d, Collin_Battery_Holder_Square v2 v2.f3d, Collin_Corner Connector 1 v2 v1.f3d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]
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2022-09-02 Update wiring diagrams to include connector images, highlighting pin 1 Fix reversed order connectors.
    [Blimpy_wiring.yml]
2022-09-08 Configure rangefinder on pixracer
    [ArudPlaneConfiguredParams.param]
2022-09-08 Configure pixracer to auto-arm and allow safety switch to unsafe
    [ArudPlaneConfiguredParams.param]
2022-09-08 Configure telem2 port on pixracer to talk to OpenMV
    [ArudPlaneConfiguredParams.param]
2022-09-08 Configure pixracer servo outputs to pass through rc/mavlink channels directly. This removes need to use Arduplane kinematic model and control algorithms
    [ArudPlaneConfiguredParams.param]
2022-09-08 Update pixracer system modified sensor offsets since last parameter backup
    [ArudPlaneConfiguredParams.param]
2022-09-08 Add attitude correction to LIDAR distance processing
    [processing.py]
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2022-09-09 Map RC controller funtions/channels to blimp functions
    [RC Mapping.csv]
2022-09-09 LIDAR mount
    [TFMini mount v2.f3d, TFMini mount v2.step, TFMini mount v2.stl]
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2022-09-09 Fix pinout on LIDAR due to incorrect manufacturer documentation Adjust cable lengths based on as-built TODO fix battery connections
    [Blimpy_wiring.bom.tsv]
2022-09-09 minor fix to sensors
    [sensors.py]
2022-09-14 Update wiring with battery connector breakout Improve terminology consistency
    [Blimpy_wiring.bom.tsv]
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2022-09-16 fixing syntax and other conflicts.
    [groundStation.py, main.py, mavlink.py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]
2022-09-16 fixed collectData when no data is avaialable
    [sensors.py]
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2022-09-23 added parts list for current build
    [Nov_22_Parts_List.xlsx]
2022-09-23 moved old files to subfolder
    [Parts_List.xlsx, PiZero_ESC_pin_diagram.xlsx, Purchase_history.xlsx]
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2022-09-23 prevent blocking for uart.
    [mavlink.py]
2022-09-23 Bugfixes from Hardware Testing
    [copySupportFilesToCamera.py, main.py, mavlink.py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]
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2022-09-23 Add QGroundControl version of configured Ardupilot parameters. Removed unused param files
    [ArduCopterConfiguredParams_forESCFlashing.param, ArudPlaneConfiguredParams.params]
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2022-09-30 lidar working over mavlink. added fix to typo of mavlink parse. prior to adding logger object
    [copySupportFilesToCamera.py, hardware.py, hardwareMock.py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]
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2022-09-30 Fixed paths and general bugfixes
    Prettied path code in main.py, as well as implemented proper pathing for testLogger.py. Additionally, fixed some bugs in MissionCommander.py, imageProcessing.py, and resolved weird merge issue with dataClasses.py
    [dataClasses.py, imageProcessing.py, main.py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]
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2022-09-30 Updated 3D models with latest versions
    [PixRacer Mount v2.step, PixRacer Mount v2.stl, PixRacer Mount v3.step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]
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2022-09-30 ImageProcessing.py Correction
    Uploaded correct version of image processing file to find goals and balls. Created a branch to stop conflicts
    [imageProcessing.py]
2022-09-30 lots of merge conflicts and minor bug fixes. printing now the hover pid
    [dataClasses.py, flightActions.py, flightDirector.py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]
2022-09-30 fixed mocking with latest changes
    [debugRoutes.js, flightActions.py, groundStation.py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]
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2022-10-02 bug, not reading requestedState from server correctly
    [dataClasses.py, missionCommander.py]
2022-10-03 Update imageProcessing.py
    Corrected variable names for tracking the closest ball and goal
    [imageProcessing.py]
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2022-10-07 fixed path in copySupportFiles and added limits to pid output
    [copySupportFilesToCamera.py, flightActions.py, mavlink.py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]
2022-10-07 added test.params
    [test.params]
2022-10-07 Change ardupilot thrust motor reverse flag. Changed thrust prop to a CCW style. All props are now CCW. PWM to ESC to motor convention will now be that 1900us PWM will spin the motor CCW as seen when 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
    [ArudPlaneConfiguredParams.param]
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2022-10-07 Fixed elsewhere before merge
    [flightActions.py]
2022-10-07 Ball Detection Metrics
    Uploading Metrics for detecting the ball in a .csv file, to quantify performance of ball detection algorithms.
    [Ball Detection Metrics.csv]
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2022-10-21 Battery cable updates
    [Blimpy_wiring.bom.tsv]
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2022-11-03 fixed variable mavlink uart read issue.
    [hardware.py, mavlink.py]
2022-11-03 last state prior to trying pid tuning for real w/ mavlink solved
    [dataClasses.py, flightActions.py, main.py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]
2022-11-03 fixed bug in lidar distance logging
    [debugRoutes.js]
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2022-11-04 ready to integrate video processing code
    [first hover success parameters.txt]
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2022-11-04 switches working for remote. csv file has channells mixed up for auto. doesn't map what is actually programmed on remote
    [main.py, missionCommander.py, sensors.py]
2022-11-04 Fixed loop issue in detect ball, where EMA updated on every blob, instead of just the largest
    [imageProcessing.py]
2022-11-04 Reworked image functions for loop issues, fixed sensor resolution in hardware
    [imageProcessing.py, sensors.py]
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2022-11-06 upload new code to open mv works from button. need to add status text to UI and error text posting from openMV.
    [main.py, mainWorker.py, openMvSwUpdater.py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]
2022-11-06 fixed error loop issue
    [main.py]
2022-11-06 adding toggle leds when there is an error.
    [main.py, mainWorker.py]
2022-11-07 switch now updates UI correctly
    [cameraSetup.py, flightActions.py, flightDirector.py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]
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2022-11-07 fixed another conversion error
    [processing.py]
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2022-11-07 printing yaw error
2022-11-07 fixed yaw controller. now works!
    [flightActions.py, mainWorker.py, openMvSwUpdater.py]
2022-11-07 fixed backwards sign for yaw error
    [flightActions.py, pidModule.py]
2022-11-07 fixed switch mode
2022-11-07 fixed hover assisted matrix
    [missionCommander.py]
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2022-11-08 swapping door actions to be correct.
    [flightDirector.py, hardware.py]
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2022-11-08 Corrected for NONE in lidar data
    [flightActions.py, imageProcessing.py, processing.py]
2022-11-08 error trapping for None
    [processing.py]
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2022-11-08 Fixed issues with image processing from conflicting merging text
    [imageProcessing.py]
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2022-11-08 Updated Green Threshold
    Issues differentiating green and yellow.
    [imageProcessing.py]
2022-11-08 adding test flight data. use v3 Martin.
    [testFlight11_8_22 v2.csv, testFlightData11.8.22 v3.csv]
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2022-11-09 missing files meant to add in last commit.
    [mainWorker.py, mavlink.py, missionCommander.py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]
2022-11-09 bugfix: returning wrong format for maneuver to execute
    [debugRoutes.js]
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2022-11-09 resolve a few more merge issues
    [dataClasses.py, processing.py]
2022-11-09 fixed logical comparison of nan
    [processing.py]
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2022-11-09 Corrected distance detection of balls/goals
    [imageProcessing.py, imageProcessingTestMain.py]
2022-11-09 adding test flight data
    [imuTestCompareToPixRacer.csv, testFlightData 11.9.22.csv, testFlightData11_9_22_v2.csv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]
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2022-11-10 Yaw rate fixed! flight data to prove it.
    [flightData Yaw fixed 11.10.22 10_30_22.csv, groundData 11.10.22 10am.csv]
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2022-11-10 added x error, y error for both goals.
    [dataClasses.py, debugRoutes.js, groundStation.py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]
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2022-11-11 new points doc
    [Points Breakout.xlsx]
2022-11-15 changes made when creating powerpoint
    [plotHoverDataFriAm.csv]
